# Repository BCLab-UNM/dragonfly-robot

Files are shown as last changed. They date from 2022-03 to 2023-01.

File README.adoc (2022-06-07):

= Dragonfly Build Guide

== Everything you need to build a Dragonfly Robot. 

https://github.com/BCLab-UNM/dragonfly-robot/blob/main/3DPrintedParts.adoc[3D Printed Parts]

https://github.com/BCLab-UNM/dragonfly-robot/blob/main/PurchasedPartsList.csv[Purchased Parts List]

https://github.com/BCLab-UNM/dragonfly-robot/blob/main/PhysicalBuild.adoc[Physical Build]

https://github.com/BCLab-UNM/dragonfly-robot/blob/main/SoftwareInstallationSetup.adoc[Software Installation & Setup]

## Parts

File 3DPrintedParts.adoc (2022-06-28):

= 3D Printed Parts

3D prints:

All prints are version controlled in onshape.
To generate STL files for Cura, onshape export to STL files using the following settings.  Note the Millimeter Units:

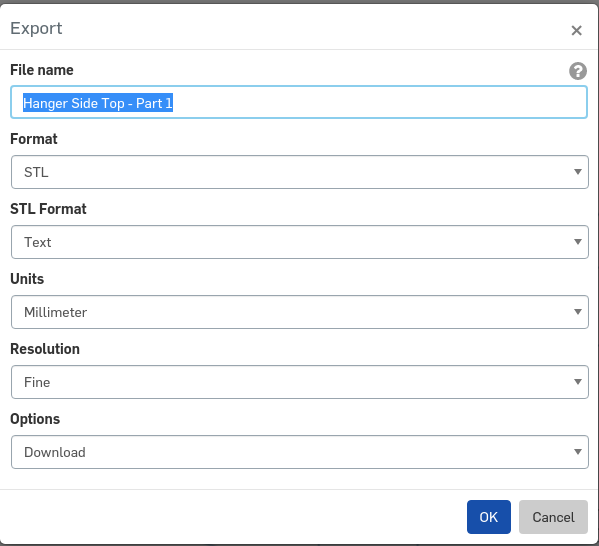
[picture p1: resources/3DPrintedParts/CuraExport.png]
Cura Export


Slice STL files with cura and print on lulzbot (lulzbot specific version of cura: https://www.lulzbot.com/cura)

== Part prints:
|===
|Part|Quantity|Picture|Notes

|Arms
|
|
|

|Arm Fulcrum
https://github.com/BCLab-UNM/dragonfly-robot/blob/main/resources/3DPrintedParts/stl/Arm%20Fulcrum.stl[STL]
|4
a|
|

|Arm Lock Lock
https://github.com/BCLab-UNM/dragonfly-robot/blob/main/resources/3DPrintedParts/stl/Arm%20Lock%20Lock.stl[STL]
|4
|
|

|ESC Mount
https://github.com/BCLab-UNM/dragonfly-robot/blob/main/resources/3DPrintedParts/stl/Motor%20Mount%20Top.stl[STL]
|4
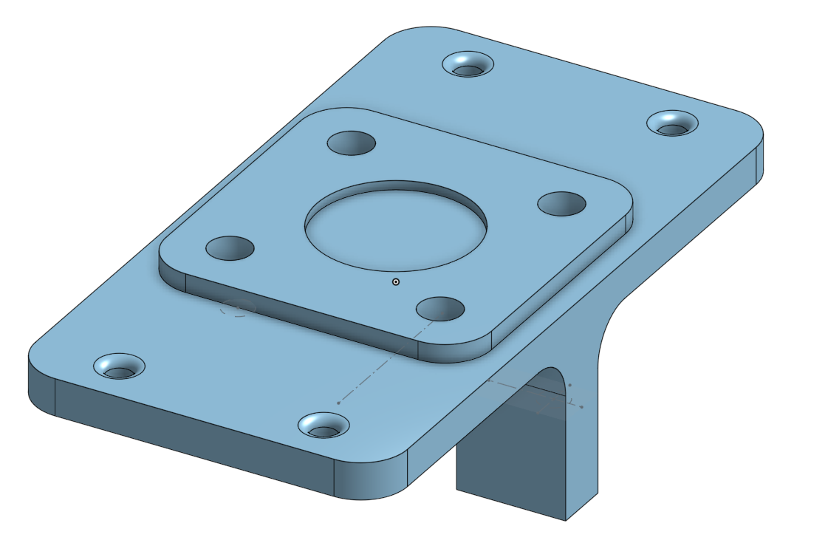
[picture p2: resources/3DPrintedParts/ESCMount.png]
a|
|

|Body
|
|
|

https://github.com/BCLab-UNM/dragonfly-robot/blob/main/resources/3DPrintedParts/stl/BH%20Clamp.stl[STL]

|Arm / Leg lock
https://github.com/BCLab-UNM/dragonfly-robot/blob/main/resources/3DPrintedParts/stl/Leg%20lock.stl[STL]
|6
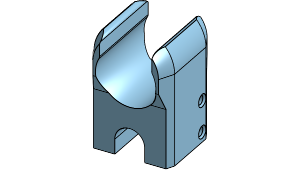
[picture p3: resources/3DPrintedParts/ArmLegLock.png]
a|
|

|Battery Tray
|
|
|

|Hanger side mount
https://github.com/BCLab-UNM/dragonfly-robot/blob/main/resources/3DPrintedParts/stl/Hanger%20Battery%20Plate.stl[STL]
https://github.com/BCLab-UNM/dragonfly-robot/blob/main/resources/3DPrintedParts/stl/Hanger%20Side%20Top.stl[STL]
|4
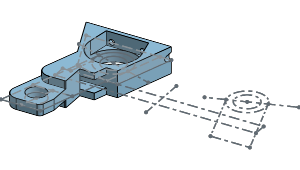
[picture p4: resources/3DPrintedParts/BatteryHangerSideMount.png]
a|
|Mirror 2 in Cura

|Hanger side bottom Left
https://github.com/BCLab-UNM/dragonfly-robot/blob/main/resources/3DPrintedParts/stl/Hanger%20Side%20Bottom%20-%20Part%201.stl[STL]
|1
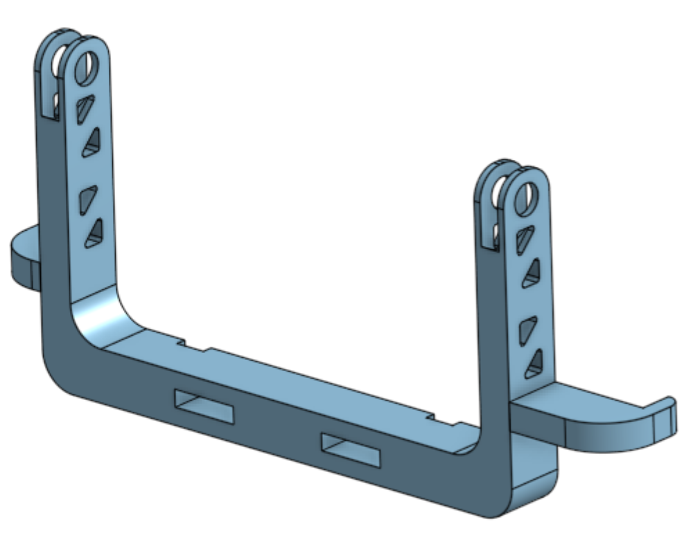
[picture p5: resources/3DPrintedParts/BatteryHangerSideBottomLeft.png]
a|
|

|Hanger side bottom Right
https://github.com/BCLab-UNM/dragonfly-robot/blob/main/resources/3DPrintedParts/stl/Hanger%20Side%20Bottom%20-%20Part%202.stl[STL]
|1
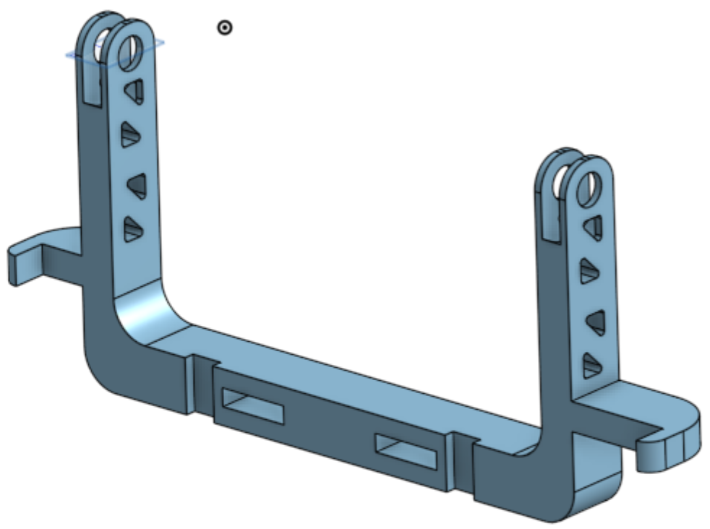
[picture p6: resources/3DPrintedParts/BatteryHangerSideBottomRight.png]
a|
|

|Axil
https://github.com/BCLab-UNM/dragonfly-robot/blob/main/resources/3DPrintedParts/stl/Axil.stl[STL]
|4
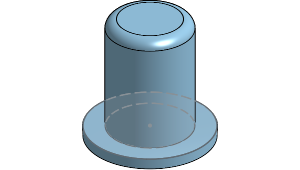
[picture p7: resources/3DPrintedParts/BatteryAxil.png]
a|
|

|Hanger brace and bracket
|2
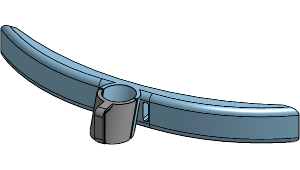
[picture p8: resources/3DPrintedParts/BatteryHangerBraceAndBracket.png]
a|
|

|Crossbeam
https://github.com/BCLab-UNM/dragonfly-robot/blob/main/resources/3DPrintedParts/stl/Cross%20Beam.stl[STL]
|2
a|
|

|Flight Controller Mount
https://github.com/BCLab-UNM/dragonfly-robot/blob/main/resources/3DPrintedParts/stl/Flight%20Controller%20-%20Top.stl[STL]
|
a|
|

|Flight controller Bottom mount
https://github.com/BCLab-UNM/dragonfly-robot/blob/main/resources/3DPrintedParts/stl/Flight%20Controller%20-%20Bottom.stl[STL]
|1
a|
|

|GPS Mount
|
|
|

|Bottom
|1
a|
|

|Screw-down
|1
a|
|

|Arm bottom
|1
a|
|Arm bottom should be cut down to allow for GPS cable to each and be able to be folded

|Arm top
|1
a|
|

|Mast stiffener
|1
a|
|

|Other
|
|
|

|Lidar mount
https://github.com/BCLab-UNM/dragonfly-robot/blob/main/resources/3DPrintedParts/stl/LIDAR%20Lite%20v4%20HP%20Holder.stl[STL]
|1
a|
|

|===

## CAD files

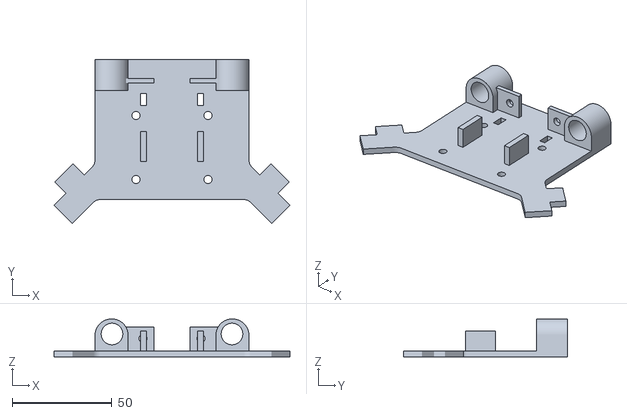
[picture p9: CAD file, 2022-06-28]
resources/3DPrintedParts/stl/LIDAR Lite v4 HP Holder.stl
118.0 x 82.0 x 19.0

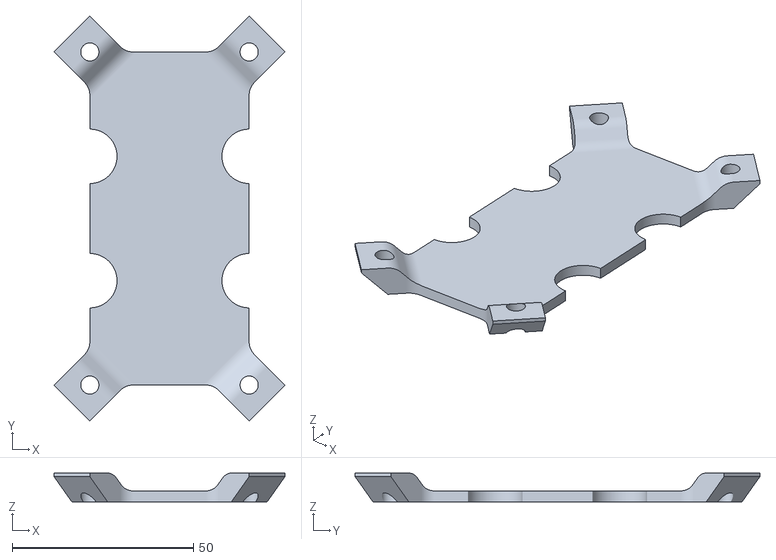
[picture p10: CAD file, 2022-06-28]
resources/3DPrintedParts/stl/Flight Controller - Bottom.stl
63.8 x 111.8 x 8.00

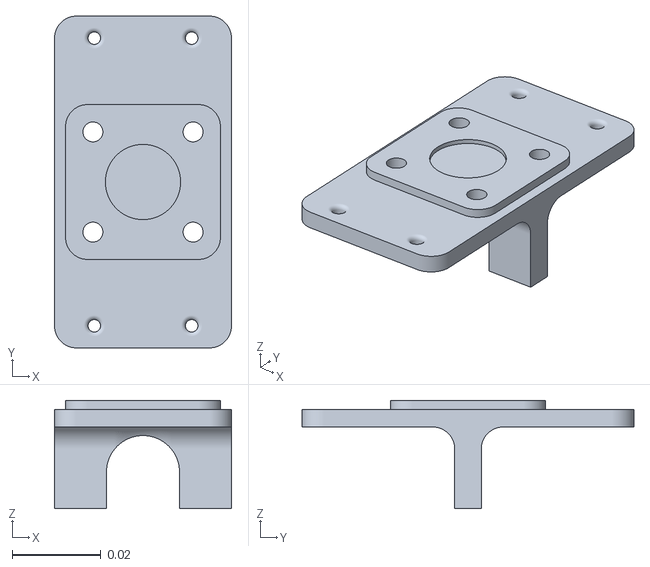
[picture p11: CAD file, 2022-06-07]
resources/3DPrintedParts/stl/Motor Mount Top.stl
0.04 x 0.075 x 0.0244

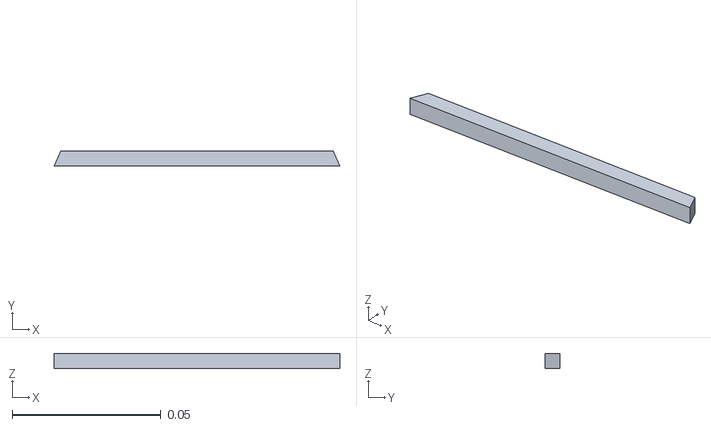
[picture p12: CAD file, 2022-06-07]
resources/3DPrintedParts/stl/Cross Beam.stl
0.0962 x 0.0052 x 0.005

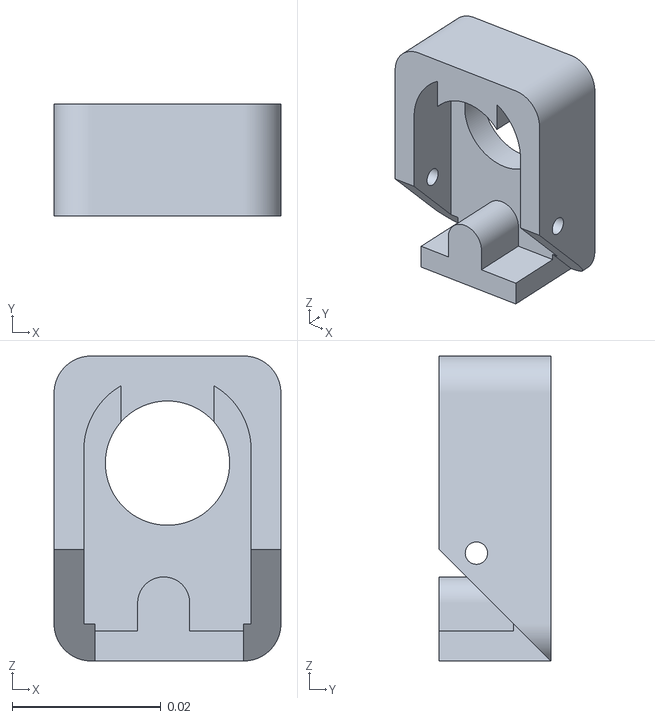
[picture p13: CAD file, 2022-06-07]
resources/3DPrintedParts/stl/Arm Lock Lock.stl
0.0305 x 0.015 x 0.041

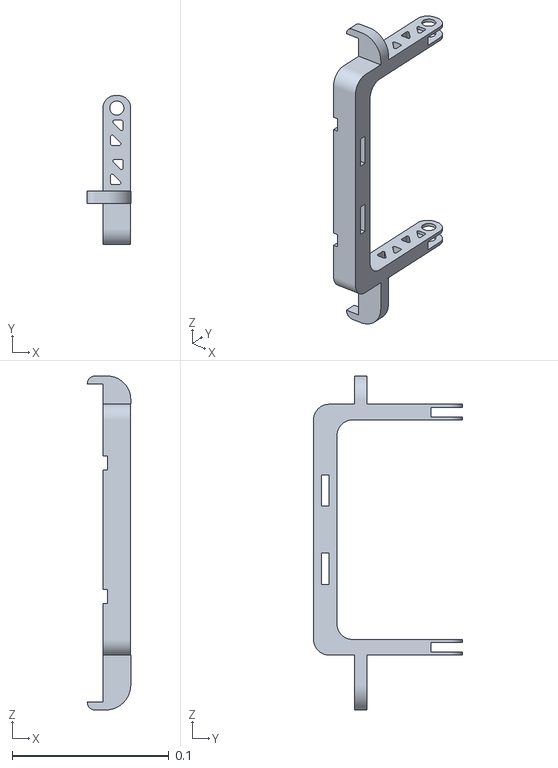
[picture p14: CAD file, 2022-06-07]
resources/3DPrintedParts/stl/Hanger Side Bottom - Part 2.stl
0.0278 x 0.095 x 0.213

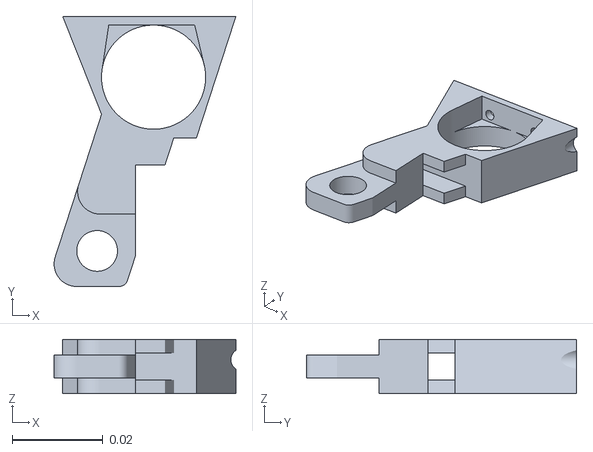
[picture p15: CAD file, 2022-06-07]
resources/3DPrintedParts/stl/Hanger Side Top.stl
0.0402 x 0.0597 x 0.012

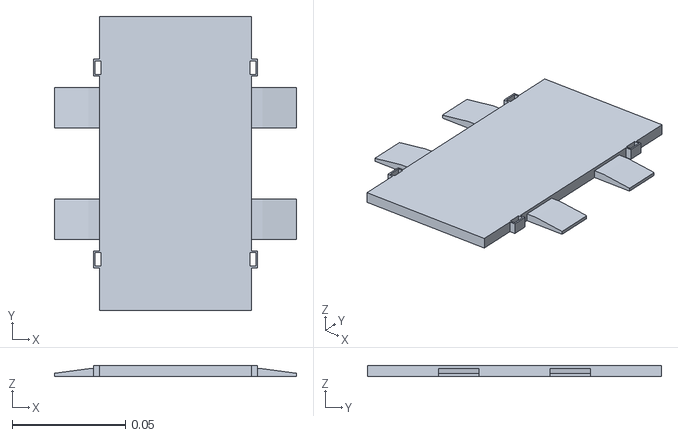
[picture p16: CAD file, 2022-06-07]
resources/3DPrintedParts/stl/Hanger Battery Plate.stl
0.107 x 0.13 x 0.005

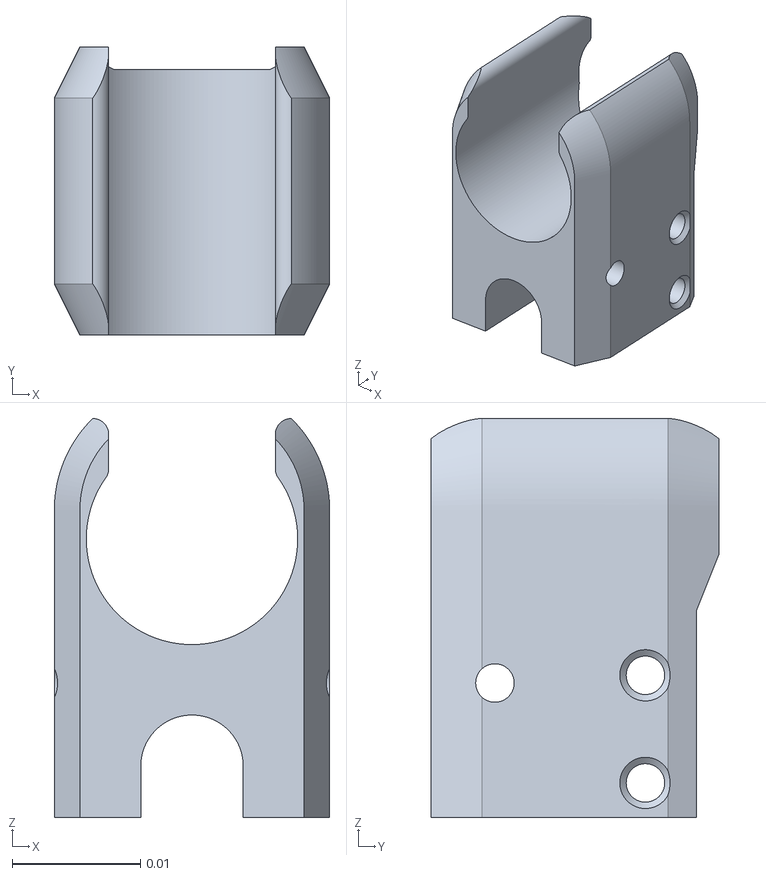
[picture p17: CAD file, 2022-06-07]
resources/3DPrintedParts/stl/Leg lock.stl
0.0215 x 0.0225 x 0.0312

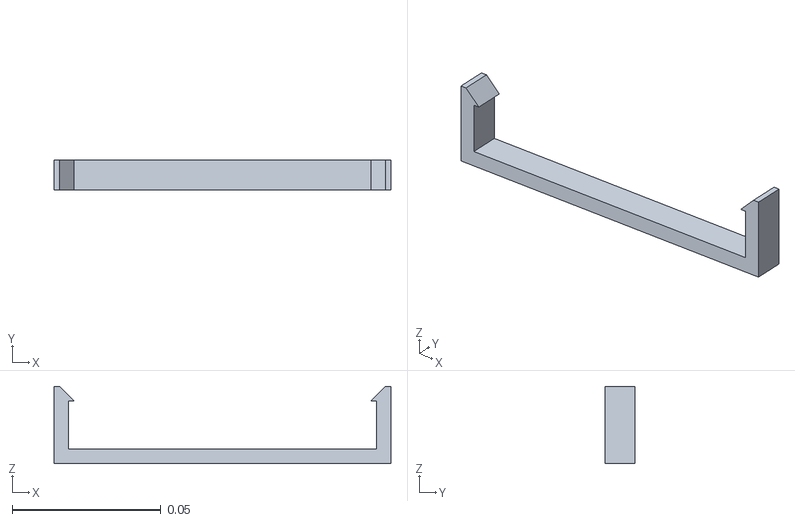
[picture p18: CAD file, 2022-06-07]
resources/3DPrintedParts/stl/BH Clamp.stl
0.113 x 0.01 x 0.026

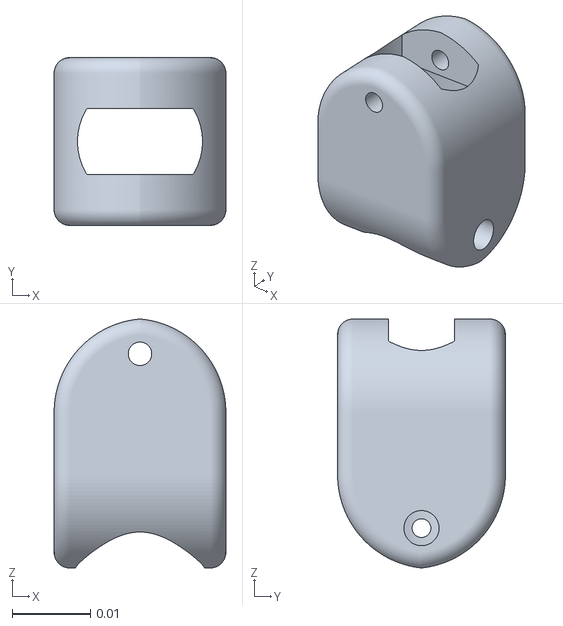
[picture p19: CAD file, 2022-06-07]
resources/3DPrintedParts/stl/Arm Fulcrum.stl
0.022 x 0.0215 x 0.0319

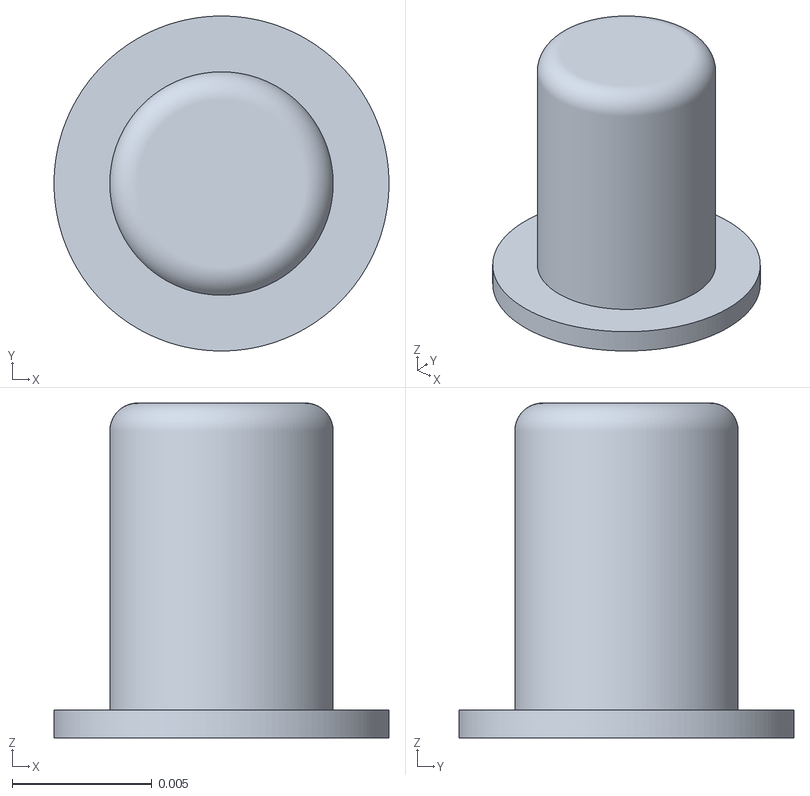
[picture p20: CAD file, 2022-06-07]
resources/3DPrintedParts/stl/Axil.stl
0.012 x 0.012 x 0.012

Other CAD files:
resources/3DPrintedParts/stl/Hanger Side Bottom - Part 1.stl

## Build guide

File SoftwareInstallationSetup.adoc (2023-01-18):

== Download and install the Raspberry Pi Imager
https://www.raspberrypi.com/software/

Ubuntu: https://downloads.raspberrypi.org/imager/imager_latest_amd64.deb

Windows: https://downloads.raspberrypi.org/imager/imager_latest.exe

== Download the image
https://cdimage.ubuntu.com/releases/22.04.1/release/ubuntu-22.04.1-preinstalled-desktop-arm64+raspi.img.xz
or #@TODO test drivers and boot time between them
https://cdimage.ubuntu.com/releases/22.04.1/release/ubuntu-22.04.1-preinstalled-server-arm64+raspi.img.xz

=== Run the Raspberry Pi Imager
Then click "CHOOSE OS" under Operating System then "use custom" then select the `ubuntu-22.04.1-preinstalled-desktop-arm64+raspi.img.xz`
Then click "CHOOSE STORAGE" under Storage and then "Internal SD card reader"
Click "WRITE" enter your password if it promts you.

Profit

After writing is compleate, mount it and edit its /etc/hostname & /etc/hosts files

=== @NOTE where it is `#` please put the appropriate number
== Edit `/etc/hostname`
edit to just
`dragonfly#`

== Edit `/etc/hosts`
just below localhost paste
`127.0.1.1 dragonfly#`

== Boot the pi up and change the password(will prompt you to do it on login),

= On the laptop/desktop

== Install ansible

== Copy over your public ssh key
from the laptops `.ssh/id_rsa.pub`
insert into `.ssh/authorized_keys`
or just run `ssh-copy-id ubuntu@dragonfly's_ip`
or just run `ssh-copy-id ubuntu@dragonfly#.local`

@Note `dragonfly#.local` might resolve

== Run the playbook from the dragonfly-controller/scripts directory
`ansible-playbook playbook.yaml -u ubuntu --inventory ./inventory`

@Note if you are getting this error below it is probably because unattended upgrades are in progress, so just wait a few minutes and run it again.

[source]
----
fatal: [dragonfly#.local]: FAILED! => {"changed": false, "msg": "'/usr/bin/apt-get upgrade --with-new-pkgs ' failed: E: Could not get lock /var/lib/dpkg/lock-frontend. It is held by process 2551 (unattended-upgr)\nE: Unable to acquire the dpkg frontend lock (/var/lib/dpkg/lock-frontend), is another process using it?\n", "rc": 100, "stdout": "", "stdout_lines": []}

----

= Install Mission Planner on Windows
https://ardupilot.org/planner/docs/mission-planner-installation.html

Connect Pixhawk to computer via USB cable

Flash Arducopter firmware and restart

Copy initial parameters from another Dragonfly and restart

Verify battery voltage.  If the battery voltage is too low (11V?) then you may need to recopy in the initial parameters.

Without propellers installed, perform a motor test.  Verify correct motor orientation and spin (reference above figure)

= Install Mission Planner on Linux (Currently broken)
Make sure exicute from inside a sub directory
[source,bash]
----
sudo apt install mono-runtime libmono-system-windows-forms4.0-cil libmono-system-core4.0-cil libmono-system-management4.0-cil libmono-system-xml-linq4.0-cil
sudo apt install mono-complete
wget https://firmware.ardupilot.org/Tools/MissionPlanner/MissionPlanner-latest.zip
unzip MissionPlanner-latest.zip
mono MissionPlanner.exe
----

= Transmitters
## Download the companion applicaiton
https://www.open-tx.org/downloads click the most recent at the top then scroll to the bottom and under `Download links:` click the appropriate installer for your system. 

== Download the SD card image
https://downloads.open-tx.org/2.3/release/sdcard/opentx-t16/

== Verify a usb connection with the transmitter
Plug in the transmitter's micro usb if you are running linux run `lsusb | grep "DFU Mode"` to verify it has come up properly if not disassemble and inspect/reseat the ribbon cable
If all is good you should see this `Bus 001 Device 036: ID 0483:df11 STMicroelectronics STM Device in DFU Mode`

== Install the downloaded opentx companion applicaiton
add the radio profile 
Radio type: Jumper T16
We have a mixture of radios so if the antenna is on the upper front then select `internalmulti` if there is the module installed below don't have it selected.
You can select `noheli` as we are running quads nto helicopters.

On the leftside make sure to download a copy of the original firmware and save it.
Make sure to click `show details` and read as you will get a `Flashing done` message even when it fails

Then `Write Firmware to radio` again make sure that the `show details` checkbox is checked and read the output to make sure the flashing completed

Unplug the transmitter and remove the sd card, make a copy of its contents, wipe it clean and then write to it the extracted files from what you downloaded in part `Download the SD card image`

Reinstall the SD card and power up the transmitter and calibrate the analogs

=== External antenna module
In the case of TX1 it does not have an internal module and the external module was running an old bootloader that did not support upgrading the firmware from the transmitter.
So Plug directly into the external module's USB micro at the bottom the the transmitter and plug into a linux system
Run `lsusb` you should see something like `Bus 001 Device 045: ID 10c4:ea60 Silicon Labs CP210x UART Bridge`

Download the module's new firmware
https://github.com/pascallanger/DIY-Multiprotocol-TX-Module/releases/download/v1.3.3.7/mm-stm-serial-reta-v1.3.3.7.bin
For a current list go to 
https://downloads.multi-module.org/

==== Install Flash multi
Fallow the instructions on
https://github.com/benlye/flash-multi/blob/master/doc/Linux.md

You'll end up running something like

[source,bash]
----
wget https://github.com/benlye/flash-multi/releases/download/0.6.1/flash-multi-0.6.0.tar.gz
tar -xvzf flash-multi-0.6.0.tar.gz
cd flash-multi-0.6.0
sudo ./tools/install.sh
sudo cp -v ./tools/45-maple.rules /etc/udev/rules.d/45-maple.rules
sudo chown root:root /etc/udev/rules.d/45-maple.rules
sudo chmod 644 /etc/udev/rules.d/45-maple.rules
sudo udevadm control --reload-rules
sudo usermod -a -G plugdev $USER\nsudo usermod -a -G dialout $USER
----
`./flash-multi -f /home/carter/Downloads/mm-stm-serial-reta-v1.3.3.7.bin -p /dev/ttyUSB0`

Once you are running a more modern bootloader on the external module you can update the using the transmitter
Just copy the bin file to the onboard SD card and fallow this
https://www.multi-module.org/using-the-module/firmware-updates/update-methods#opentx

== Rebind the transmitter to the dragonflys
Hit the "MDL" button, then roll the right roller to the right until you get to Internal(or External) RF got to mode change to `MULTI`, the next option change to `FrSky X` then the next selection to `D16 8ch` press the wheel for enter/continue
Then change the receiver number to match the dragonfly's # and then select bind, the transmitter should beep. While you are doing this power up the dragonfly and while doing so have the small button the on the X8R depressed.
then power cycle both the dragonfly and the transmitter you should have a solid green light on the X8R receiver if not try again

== Disable inactivity alarm 
Sys press the page button until you are on the Radio setup tab then scroll down to alarms and set inactivity to `0m`

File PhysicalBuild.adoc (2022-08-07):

= PhysicalBuild
:toc:

== Tiger Motor Flame 60A ESC programing cable removal mod
Using a 1.5mm hex tool unscrew the 4 bolts

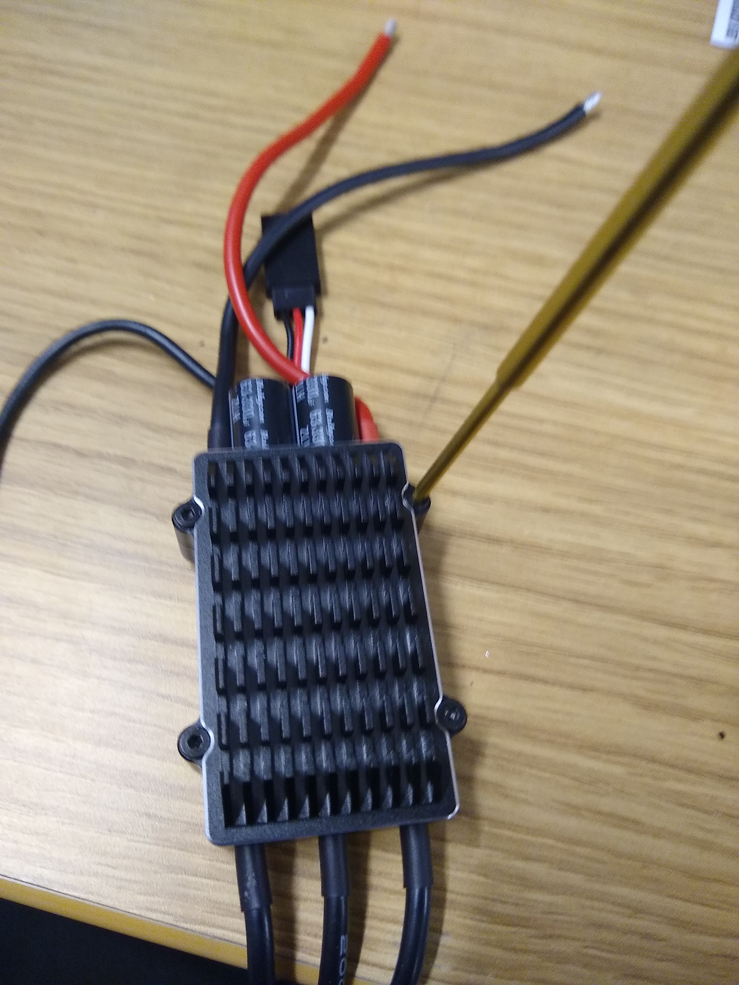
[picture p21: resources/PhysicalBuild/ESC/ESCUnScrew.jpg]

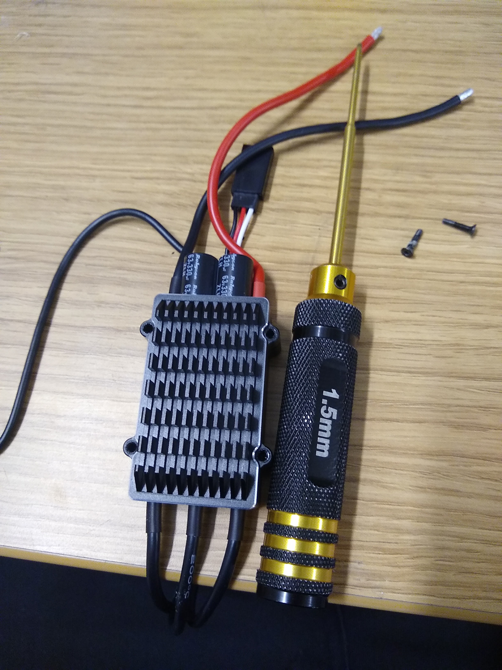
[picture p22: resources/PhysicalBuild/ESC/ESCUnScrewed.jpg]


The housing should pull apart smoothly, and then carefully pick off the indicated epoxy.

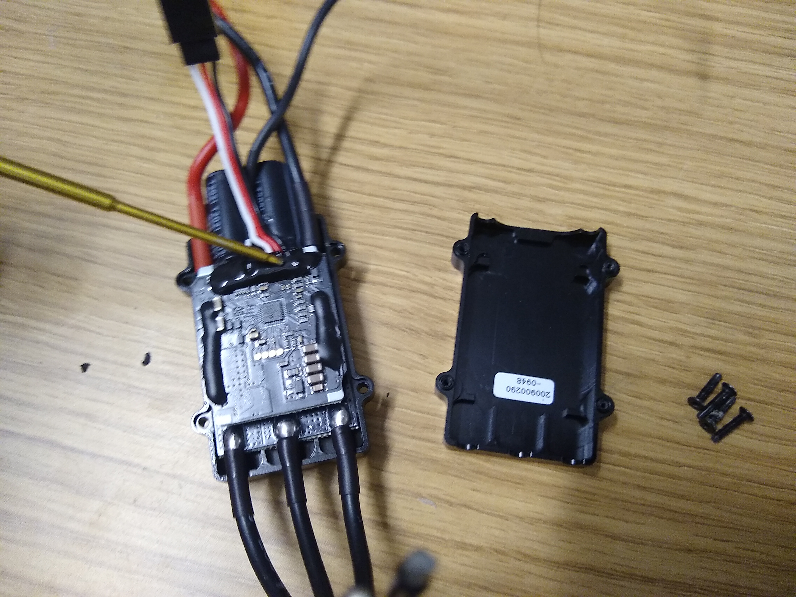
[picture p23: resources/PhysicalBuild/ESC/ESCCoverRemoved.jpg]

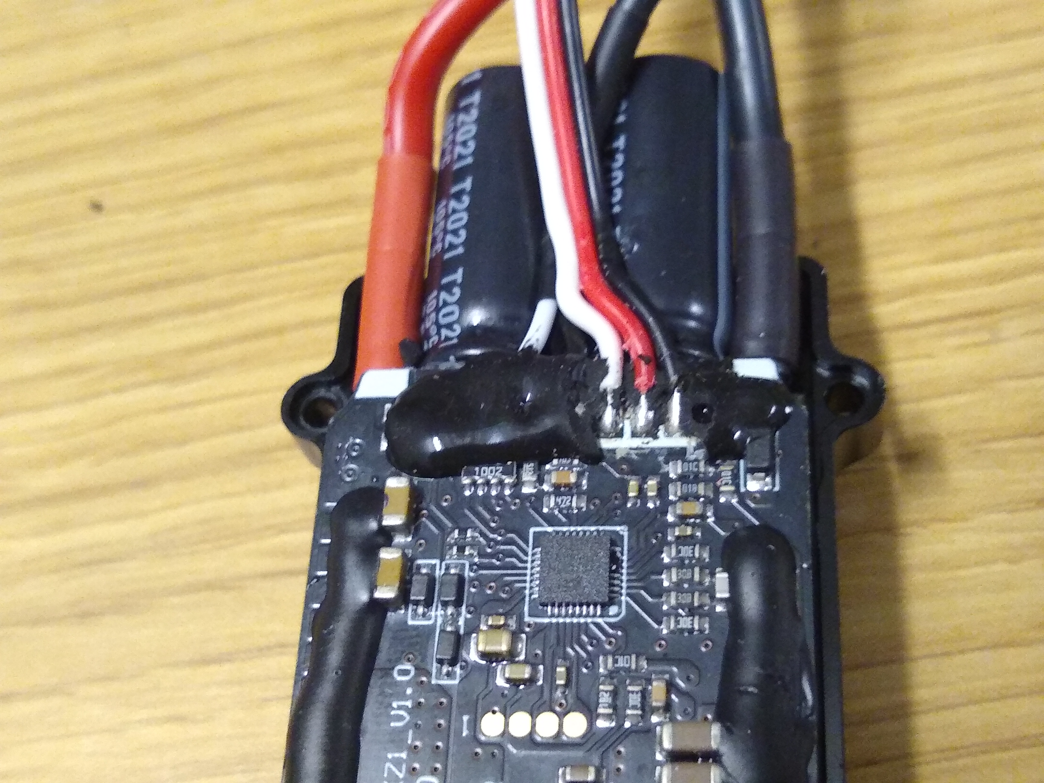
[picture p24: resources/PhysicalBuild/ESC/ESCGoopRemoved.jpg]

Use a soldering iron to reflow and remove the indicated wires, then cover the pads with hotglue.

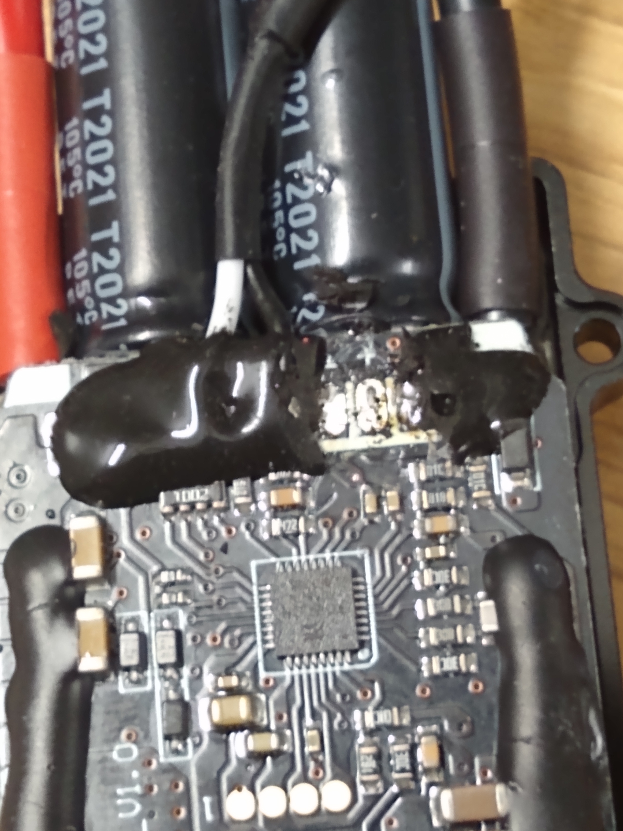
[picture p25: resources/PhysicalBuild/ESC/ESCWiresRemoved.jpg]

While the hotglue is still got place the back cover back on firmly and hold for a few seconds to cool.

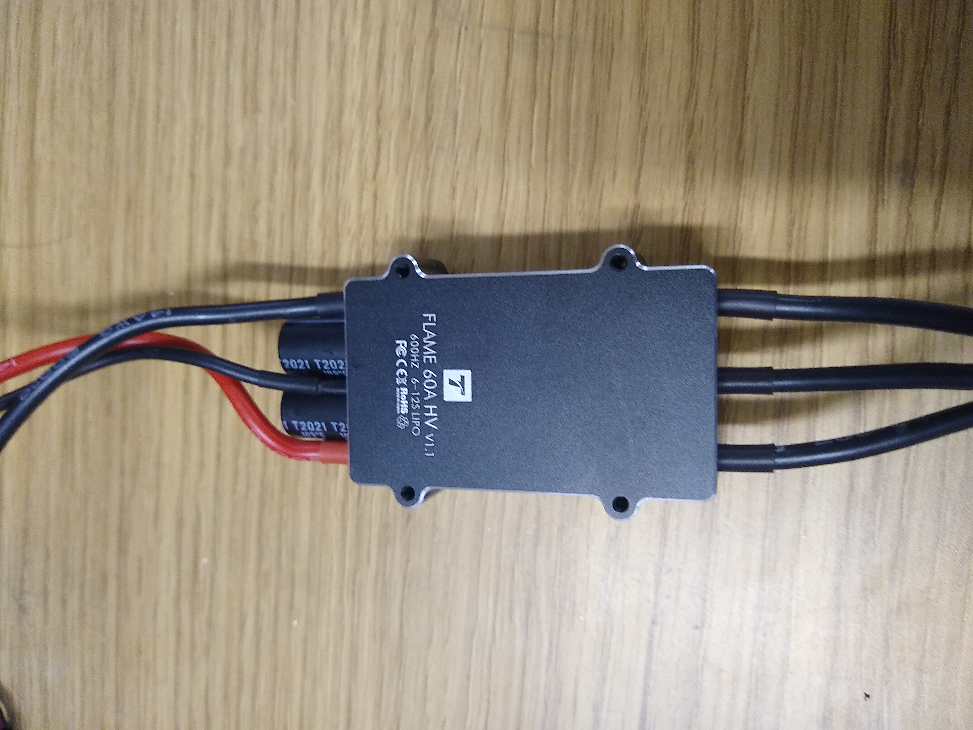
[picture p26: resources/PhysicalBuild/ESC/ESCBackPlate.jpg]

Flip back over and reinstall the bolts.

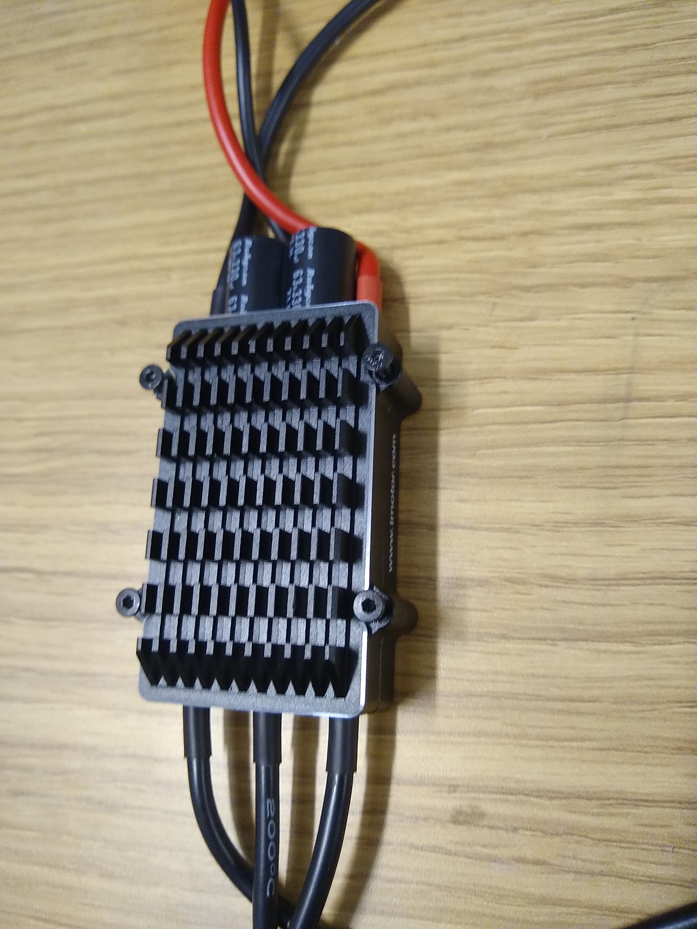
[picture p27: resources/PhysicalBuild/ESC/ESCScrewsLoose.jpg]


== Arms

Solder motors to ESCs

* 2 motors straight wired, 2 motors with 2 wires swapped.  This supports the motor orientation to hard-wire their rotation.  Make sure to add heat shrink around each solder joint.

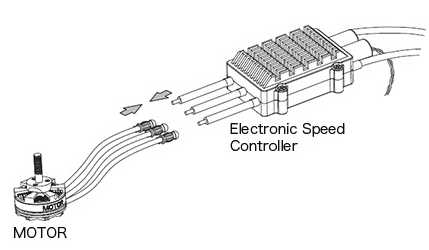
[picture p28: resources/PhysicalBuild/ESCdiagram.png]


Extend power wires from ESCs

* Add heat shrink around each solder joint



Attach Motor to motor mounts

* Make sure to attach metal brackets prior to attaching motors
* Loctite motor bolts and arm bracket bolds

Slide the plastic onto the bolt

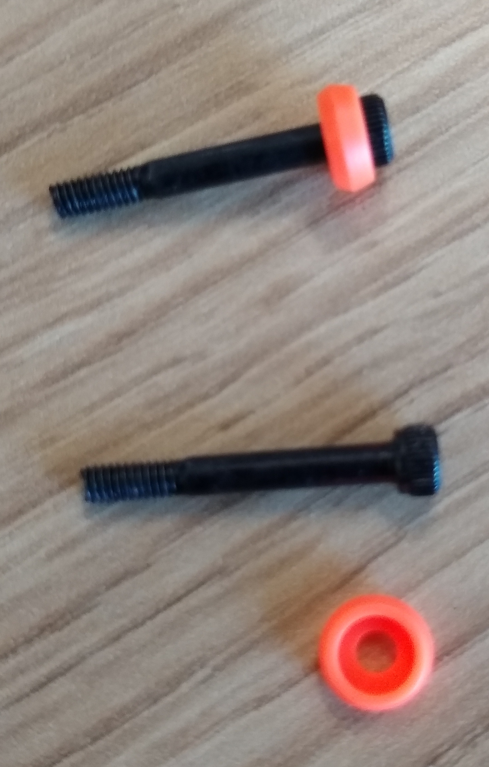
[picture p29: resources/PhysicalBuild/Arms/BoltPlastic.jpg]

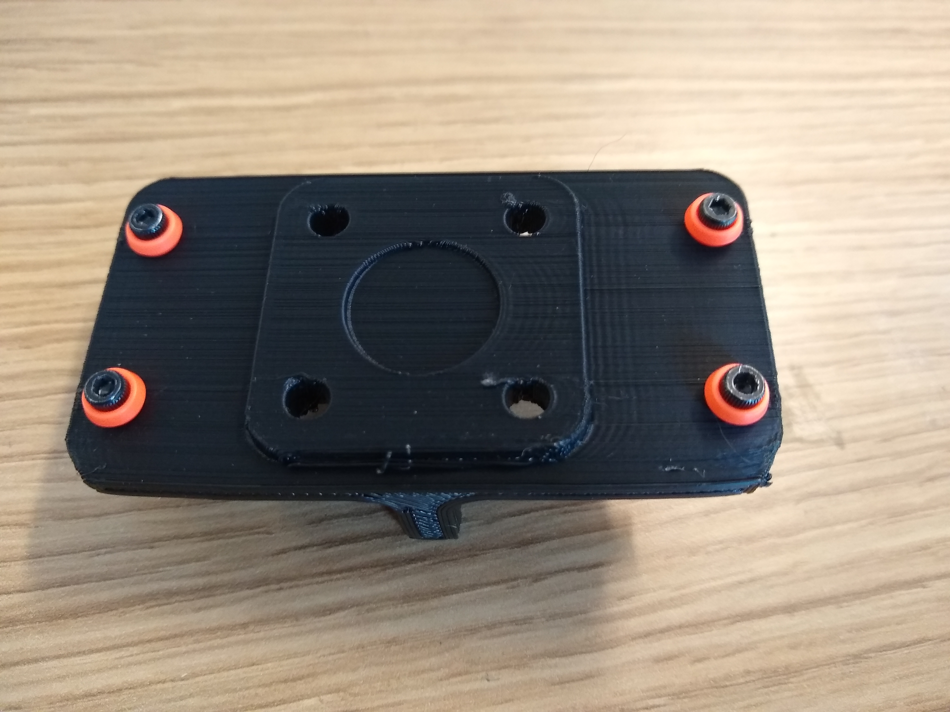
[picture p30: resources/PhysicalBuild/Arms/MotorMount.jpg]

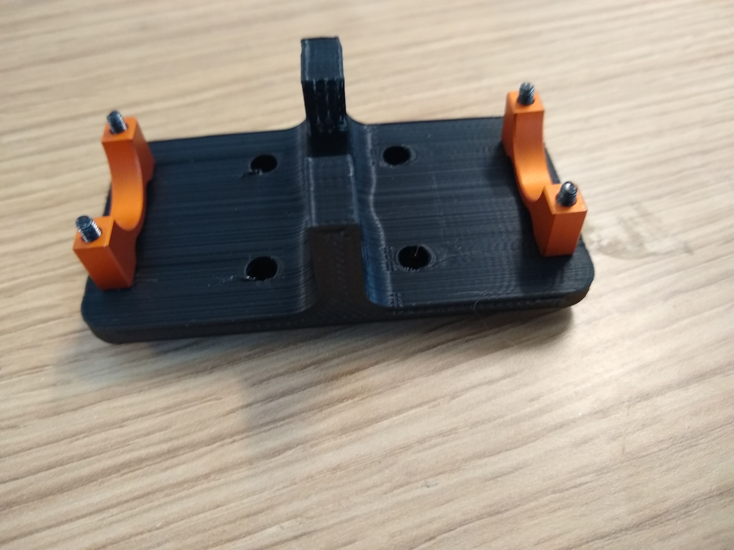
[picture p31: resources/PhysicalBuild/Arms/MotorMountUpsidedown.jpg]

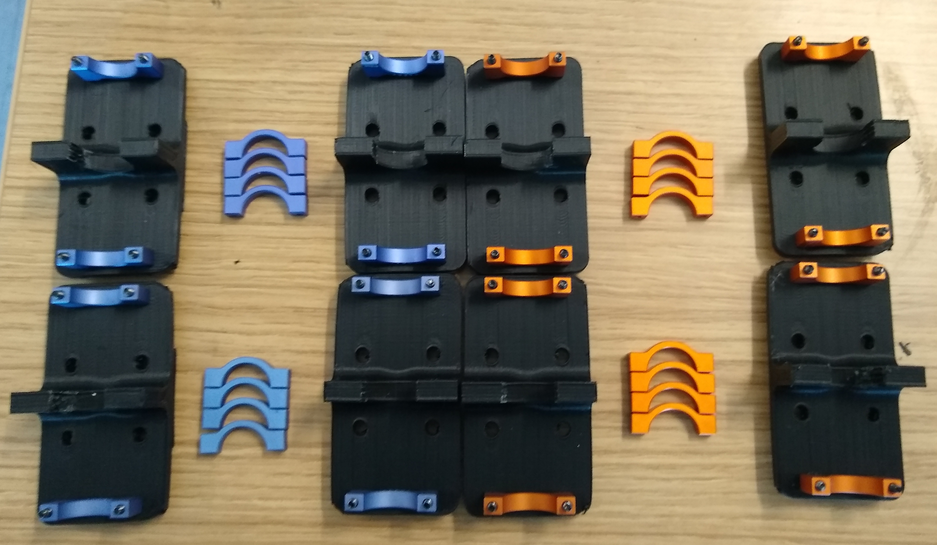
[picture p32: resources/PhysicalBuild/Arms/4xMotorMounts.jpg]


`@TODO update image`



NOTE: Wear respiration PPE when cutting or drilling carbon fiber.

Cut arm to 18 inches:



Drill a hole to attach the hinge to arm.  This hole should align with the hinge mounting holes -  to align in, you can put the hinge in place and mark a drill point.



Prepare the arm hinge 3D print by adding the brass inserts. Note the shorter brass insert is used to secure the long bolt through the arm, all the other brass inserts are the longer inserts.




Remove the bolt from the kit arms:

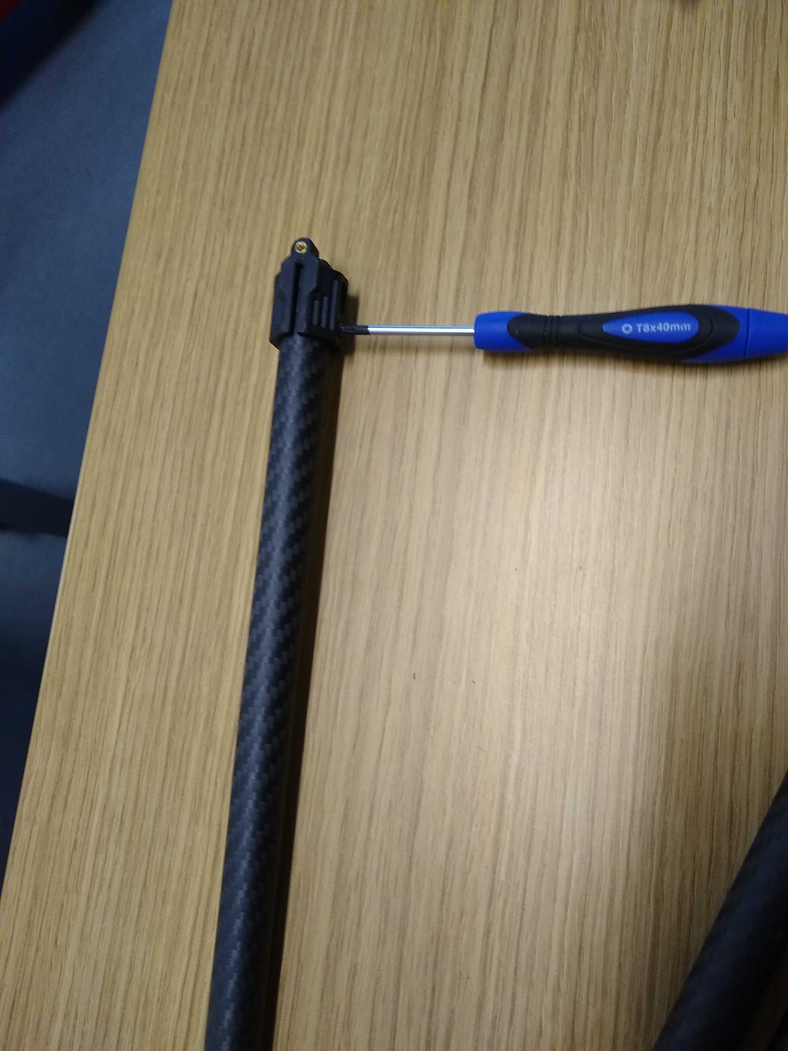
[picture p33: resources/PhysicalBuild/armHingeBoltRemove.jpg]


Attach the prepared arm hinge using the long bolt to the end of the arm:



Attach mounted motors to end of arms

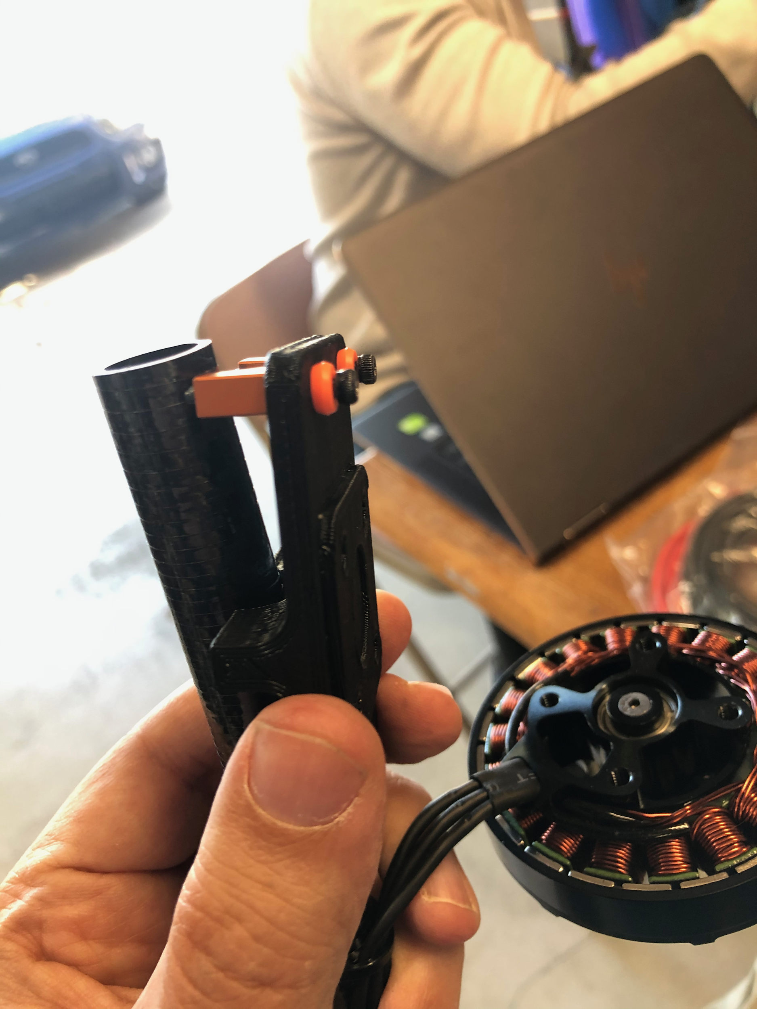
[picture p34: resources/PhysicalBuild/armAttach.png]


Zip tie ESCs to the bottom of the arm and the wires against the arms:

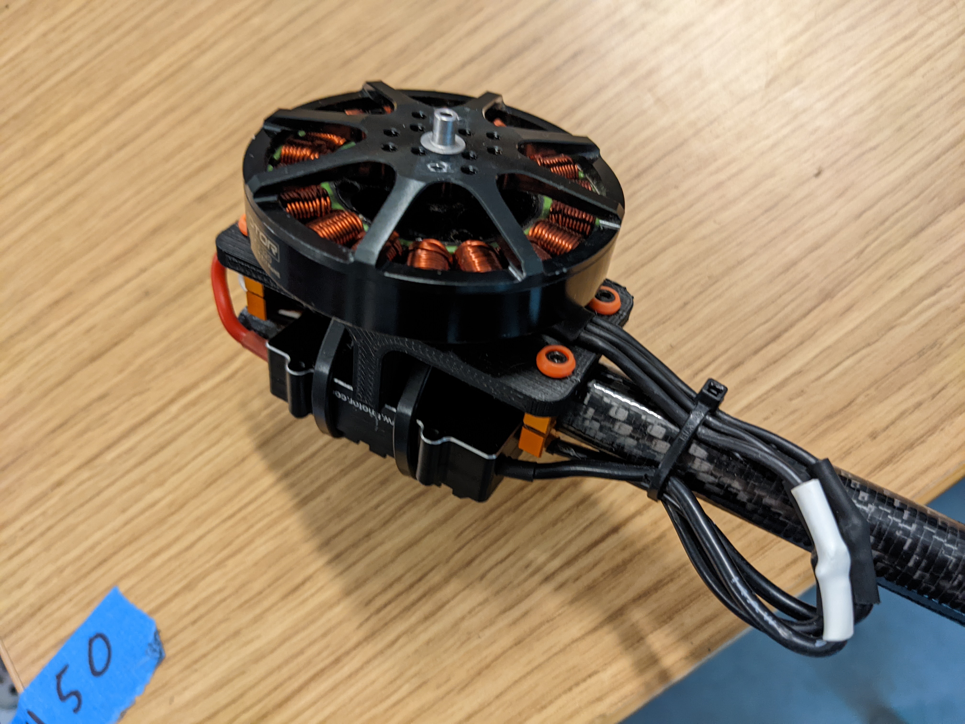
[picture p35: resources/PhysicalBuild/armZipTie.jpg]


Result
4x of these, 2 with swapped ESC / Motor wires:

`@TODO image of finished arms`

== Body

=== Legs
Cut the thicker carbon fiber tube to match the length of the provided ones in the kit.
Make sure the setscrews are installed if not look for them in a small plastic bag.
Install the tube and tighten till the tubes won't move/pullout.

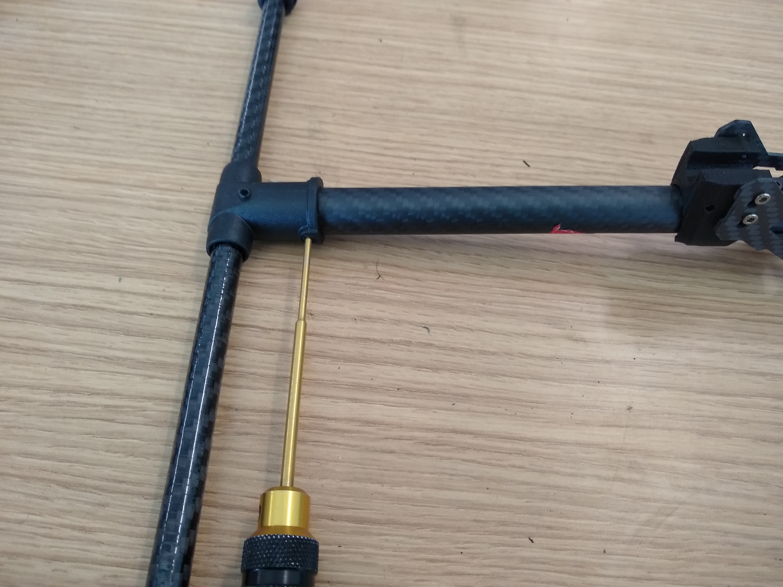
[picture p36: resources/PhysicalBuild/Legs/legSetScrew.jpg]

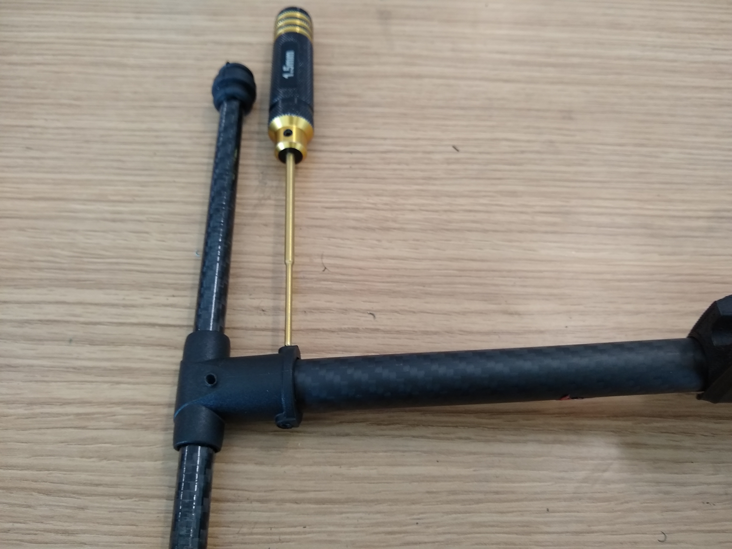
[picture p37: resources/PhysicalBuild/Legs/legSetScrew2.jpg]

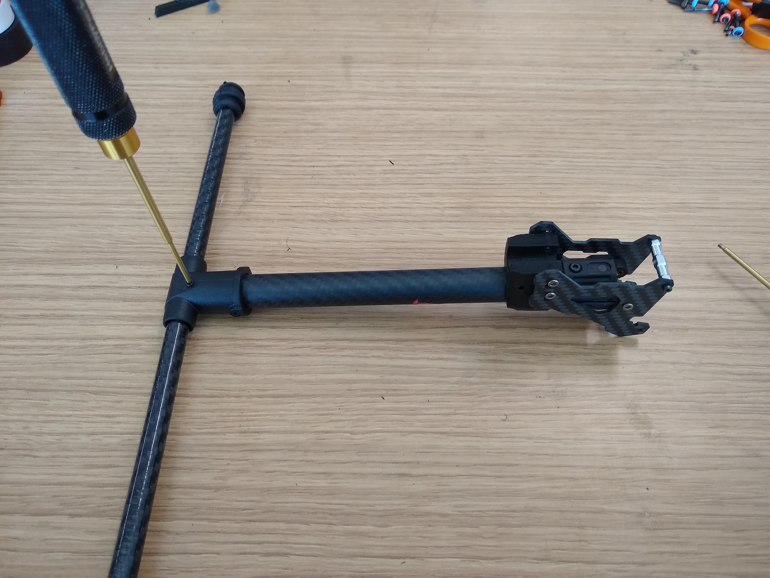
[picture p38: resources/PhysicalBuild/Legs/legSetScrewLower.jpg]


Mount Legs

Unscrew leg brackets and attach them to the body

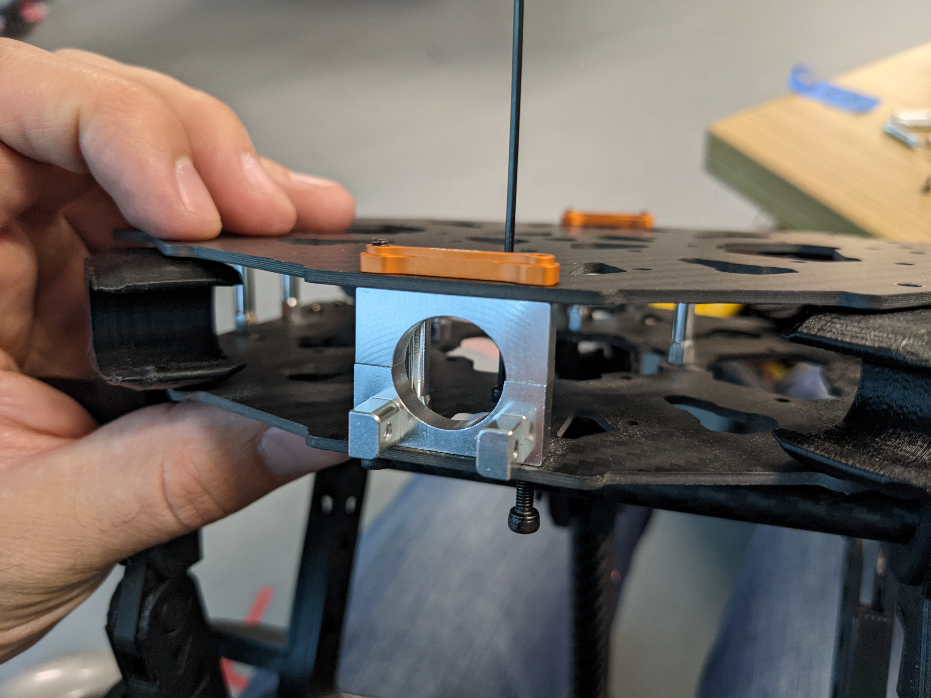
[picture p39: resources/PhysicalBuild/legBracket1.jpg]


Reattach legs to brackets and connect set screw

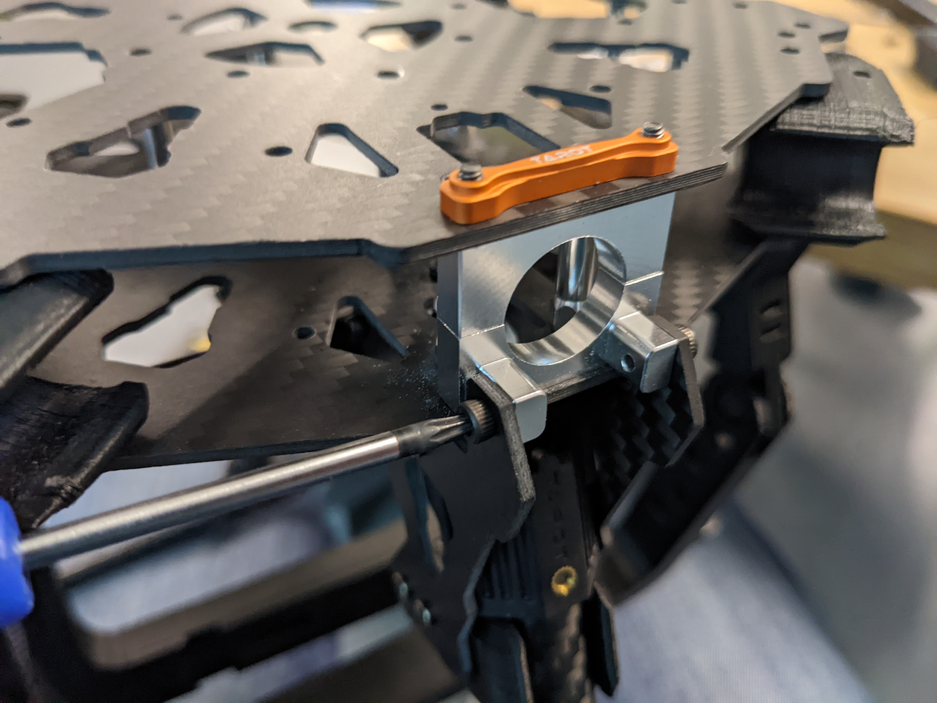
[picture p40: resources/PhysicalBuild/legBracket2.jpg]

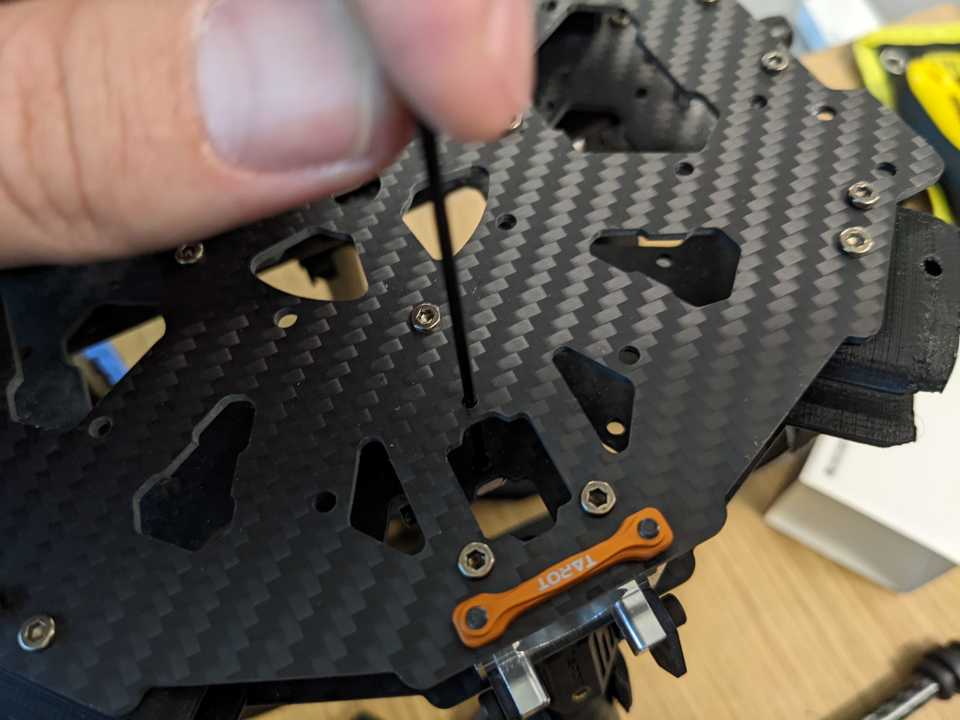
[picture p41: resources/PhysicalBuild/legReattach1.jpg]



Mount Arms

Prepare 3D printed arm clasps by inserting long brass inserts into mounting holes:

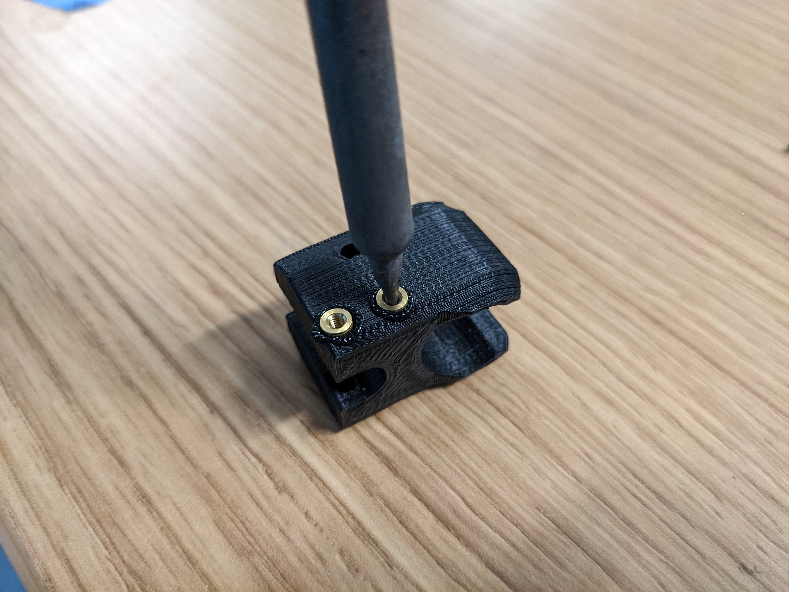
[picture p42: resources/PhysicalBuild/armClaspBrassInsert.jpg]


* Replace stock tarot frame arm locks with larger 3D printed arm clasps.


Attach built arms to attachment points in the body frame.



`@TODO missing image built arm attach`

Keep in mind motor orientation.  Motors A and C (1 and 2) should be using crossed ESC to motor wiring orientation, motors B and D should be straight. (See Quad motor letter example figure for arm labels).

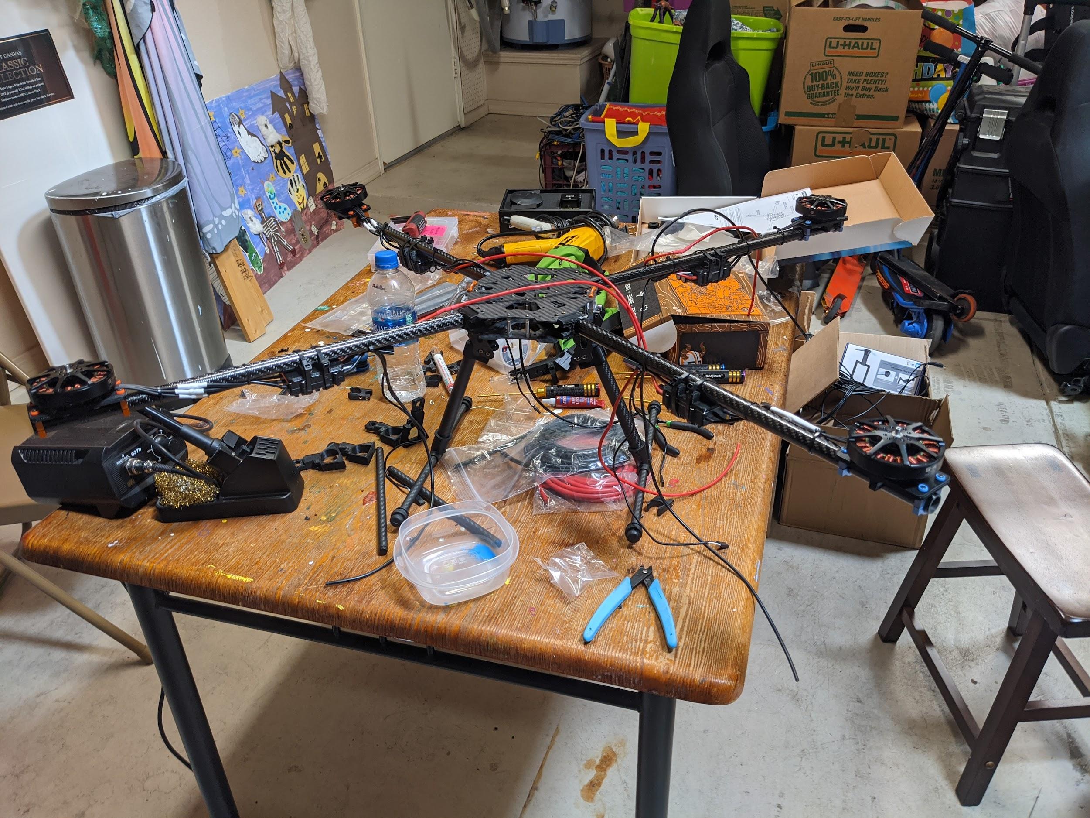
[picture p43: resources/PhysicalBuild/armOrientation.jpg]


Solder Hall Effect sensor (Mauch voltage sensor) to XT90 plug
Verify hall effect sensor orientation.  Arrow should be pointing away from the battery in, towards the quad

`@TODO missing image hall effect sensor`

Wire power to main power
Route wires into permanent locations and make sure you have enough slack
Hall Effect

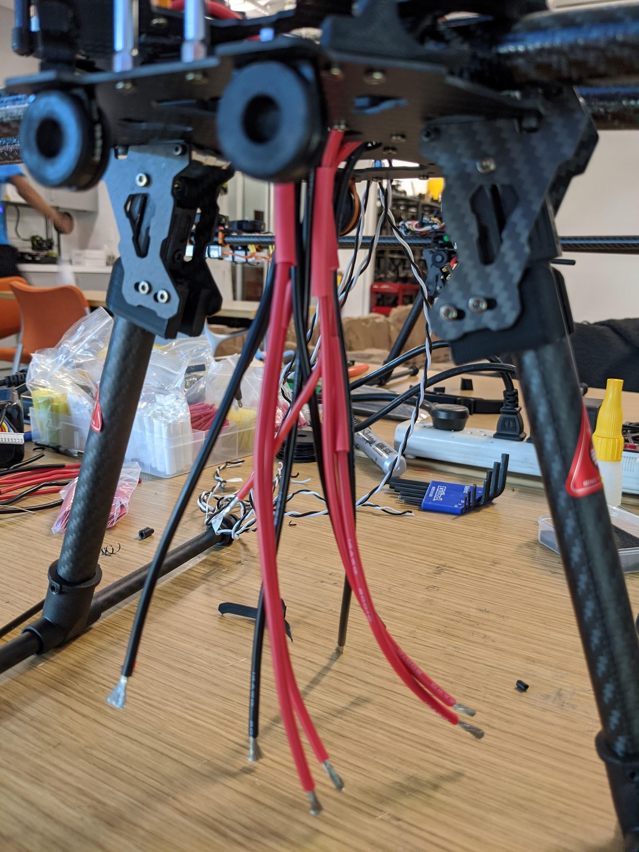
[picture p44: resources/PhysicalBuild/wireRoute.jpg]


5 power and 5 ground into 1 power 1 ground -> PL-Sensor -> Anti-spark connectors.  Add heavyduty heat shrink around joints and stow wires


Result:

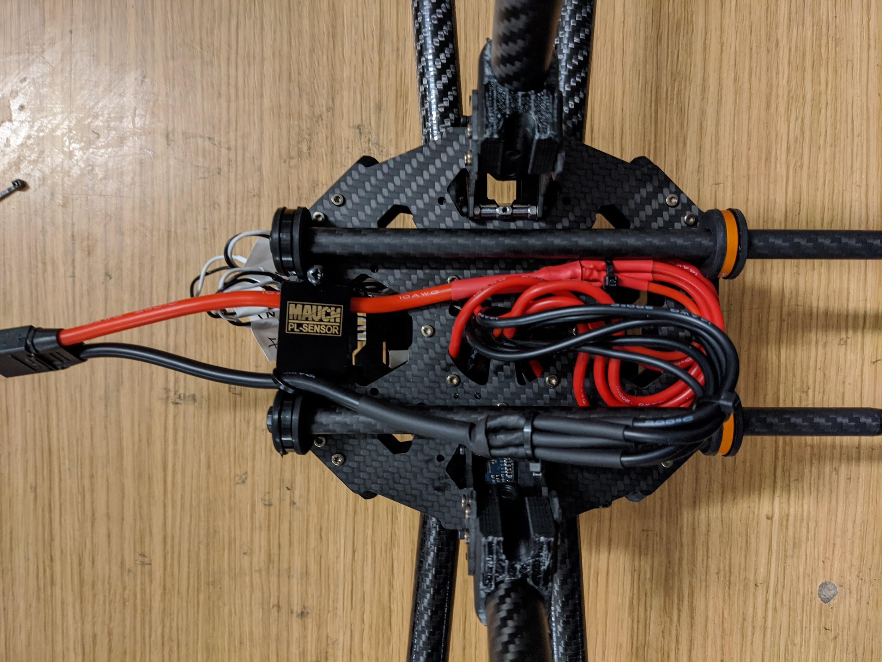
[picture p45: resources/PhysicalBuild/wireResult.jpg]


==  Battery Tray
Add Battery Tray
Attach tray hangers to body (metal payload brackets go inside of 3D printed parts):
`@TODO need image`

Add payload rails.  The long bracket end should face towards the back of the quad (weight offsets the payload)

`@TODO need image`

Attach left and right battery brackets using axils and crossbeams to stabilize separation between tray hangers.  Use a battery to ensure that the mounting separation is correct.  The battery should be fixed (not tight or loose) within the battery hangers and brackets.


Add glue to axils and crossbeams




`@TODO need image of adding glue to axils`

Mount top plate to body
Top plate should face forward with mourning fins on the left and right side of the quad.  The forward orientation of the plate has a notch for GPS mast clearance.

Make sure Mauch has enough slack

`@TODO missing image Mauch slack check`

Widen holes in body to accept bolt

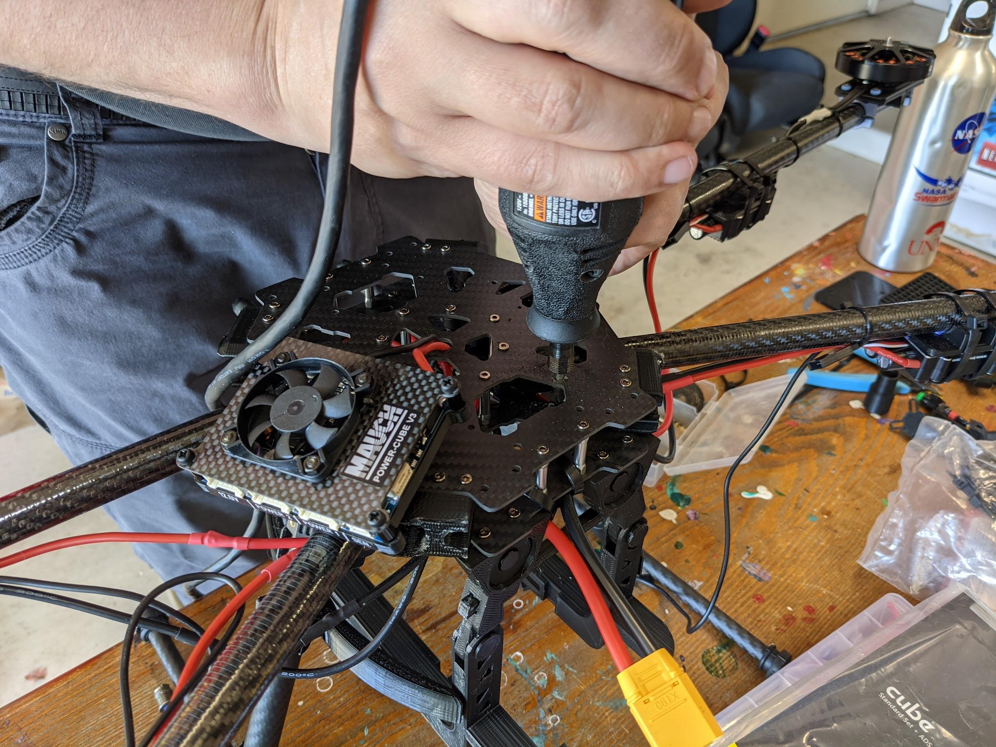
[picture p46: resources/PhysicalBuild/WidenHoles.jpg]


Screw top plate to body with rubber dampeners sandwich between top plate and body


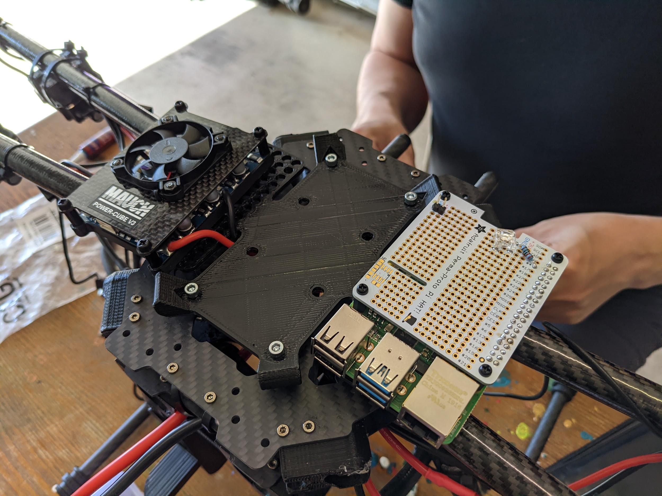
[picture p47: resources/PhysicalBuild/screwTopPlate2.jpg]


Mount pixhawk
Tape Pixhawk down to secondary top plate in corners



Glue secondary top plate to top plate with vibration gel

`@TODO need image`

== Assemble Raspberry pi

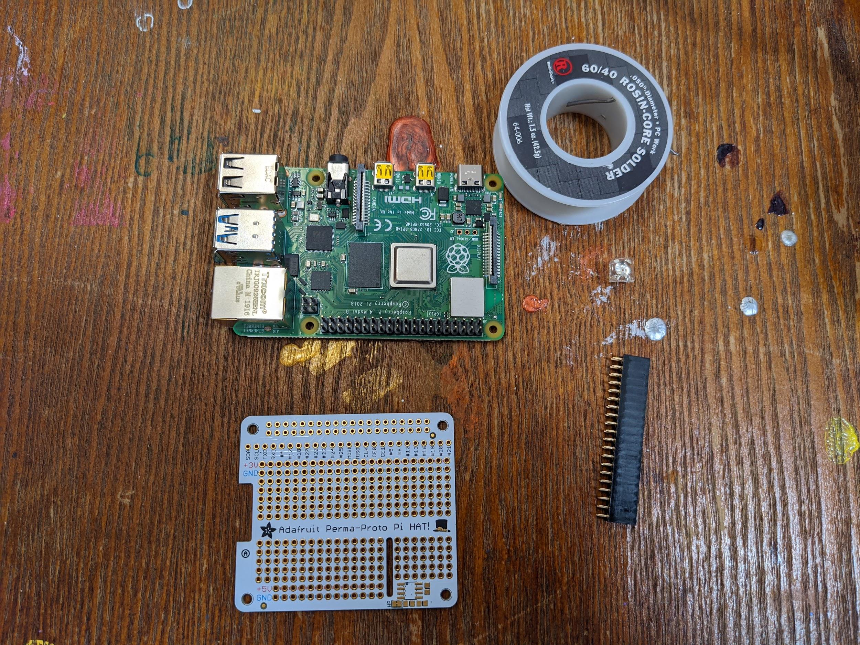
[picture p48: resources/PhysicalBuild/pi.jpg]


Solder in mounting leads

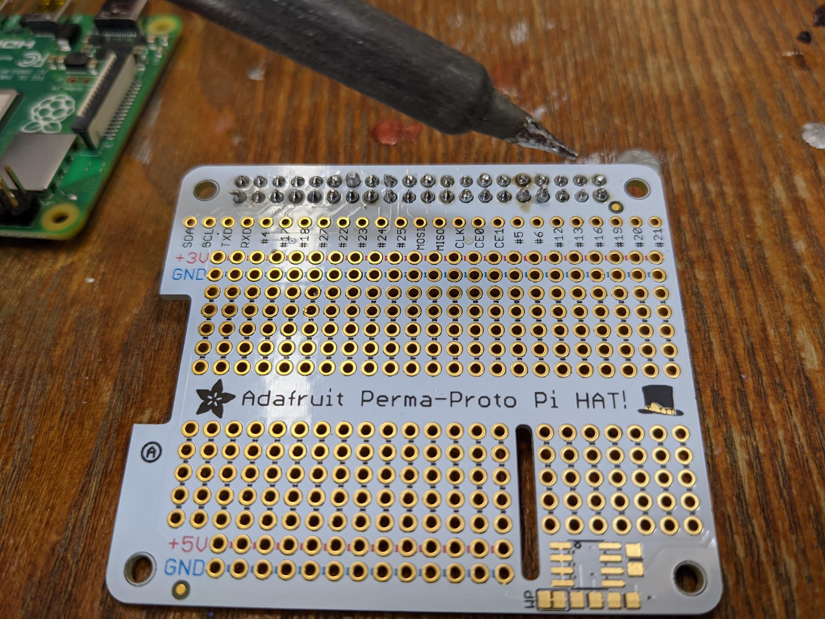
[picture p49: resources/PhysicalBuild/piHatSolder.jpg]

Wire indicator LED to hat (LED should have note facing forward)

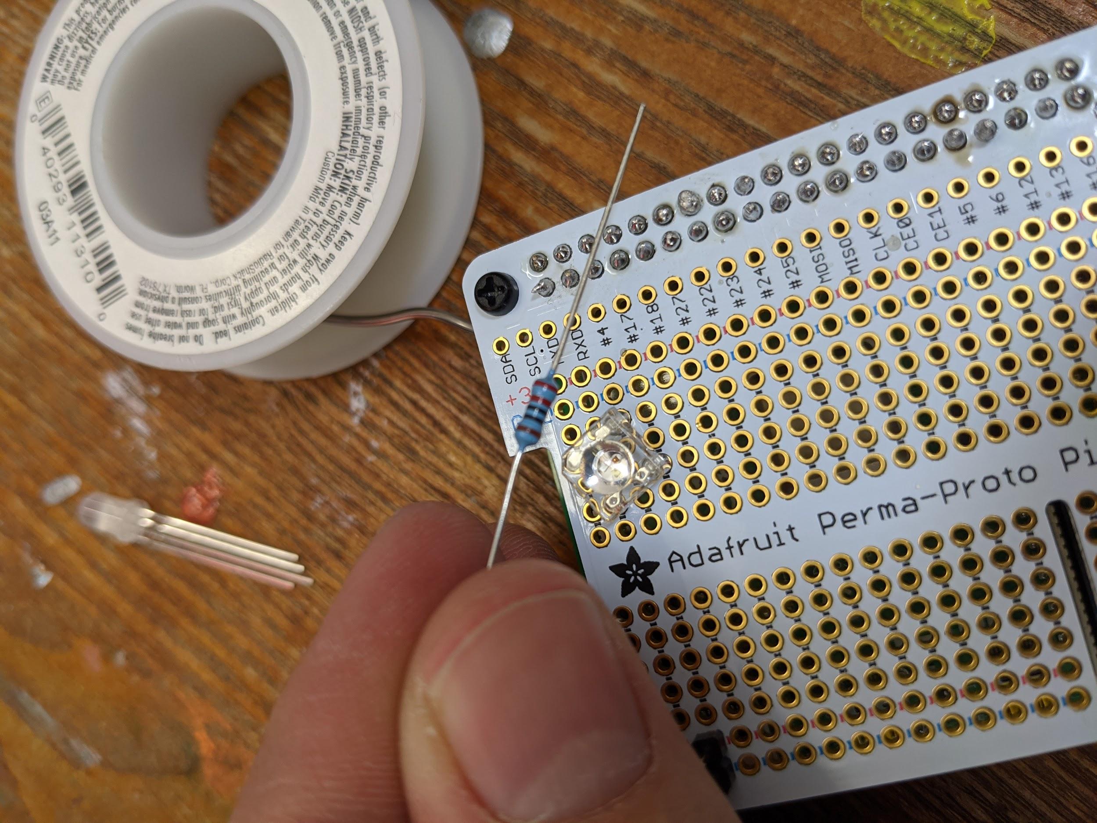
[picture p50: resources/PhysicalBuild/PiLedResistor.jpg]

Solder power jumpers

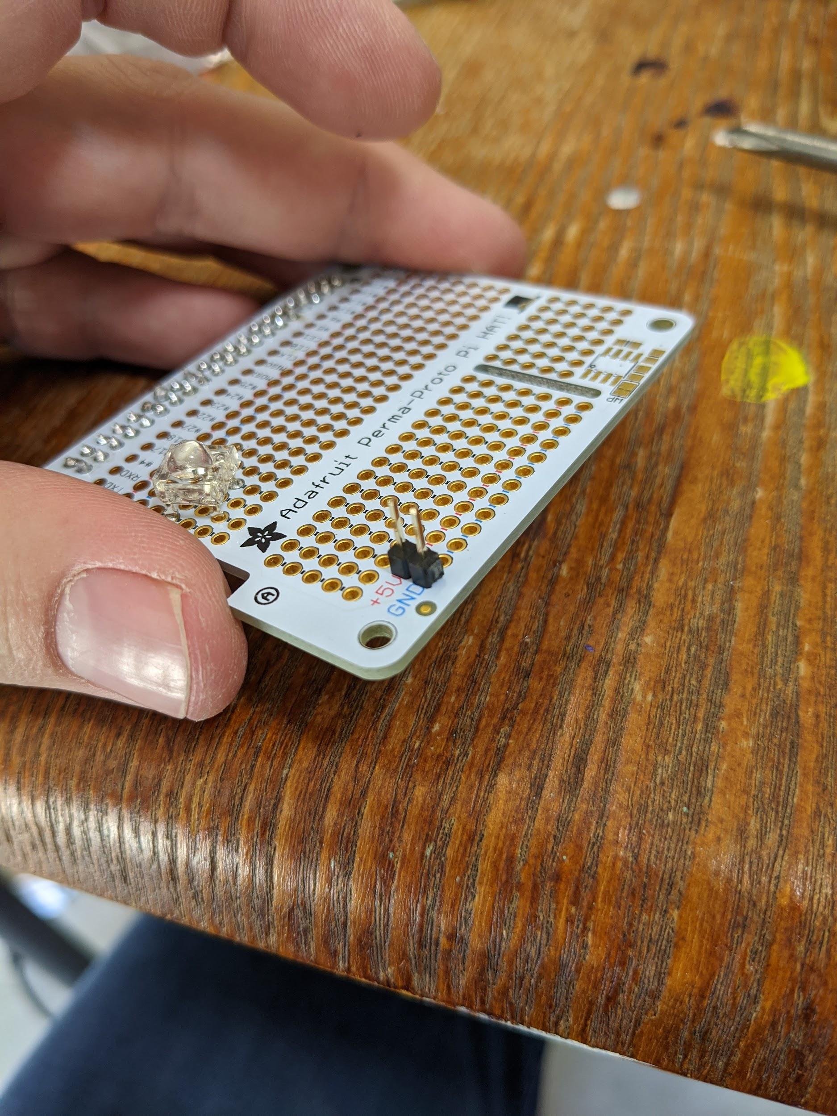
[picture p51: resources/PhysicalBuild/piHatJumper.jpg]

Attach to Raspperry PI using plastic standoffs

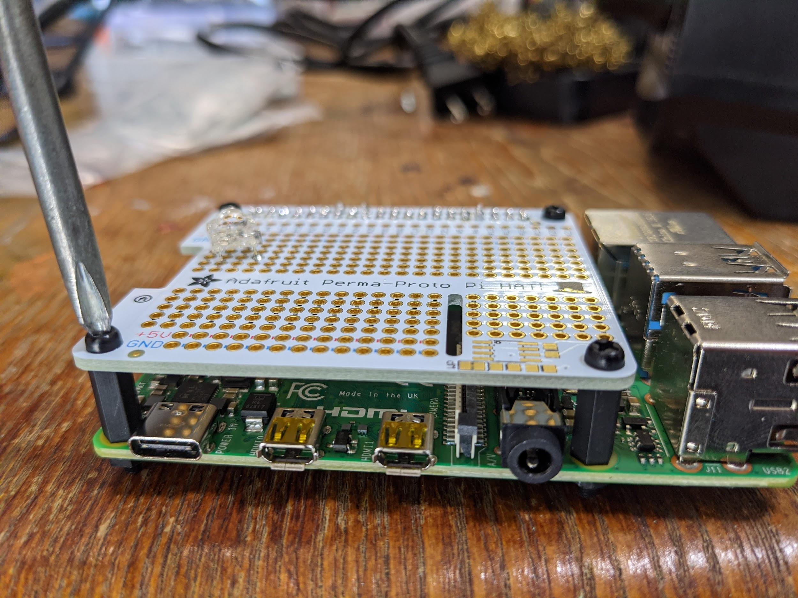
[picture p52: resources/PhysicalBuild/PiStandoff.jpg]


Ziptie down Raspberry pi
Use large ziptie as “belt”, second small ziptie in corner


Ziptie down mauch power supply
Small zip ties in 4 corners


Wire mauch to pixhawk power 1 and power 2


`@TODO double check this image`

Mount power button and wire to Mauch


Wire hall effect sensor (voltage sensor) to Mauch

`@TODO need image`

Run ESC control lines to pixhawk
The motor orientation shoudl already be set, but wiring the control lines tot he pixhawk must be done in the specified order: [A,C,D,B] -> [1,2,3,4]

https://ardupilot.org/copter/docs/connect-escs-and-motors.html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

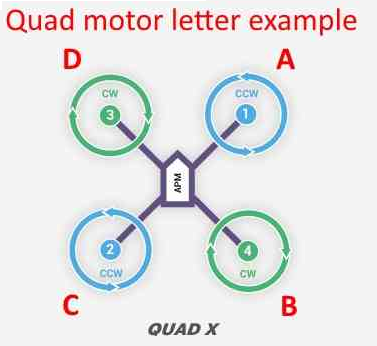
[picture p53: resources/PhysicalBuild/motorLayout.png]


Wire telemetry and radio control to pixhawk, velcro to the bottom

`@TODO need image`

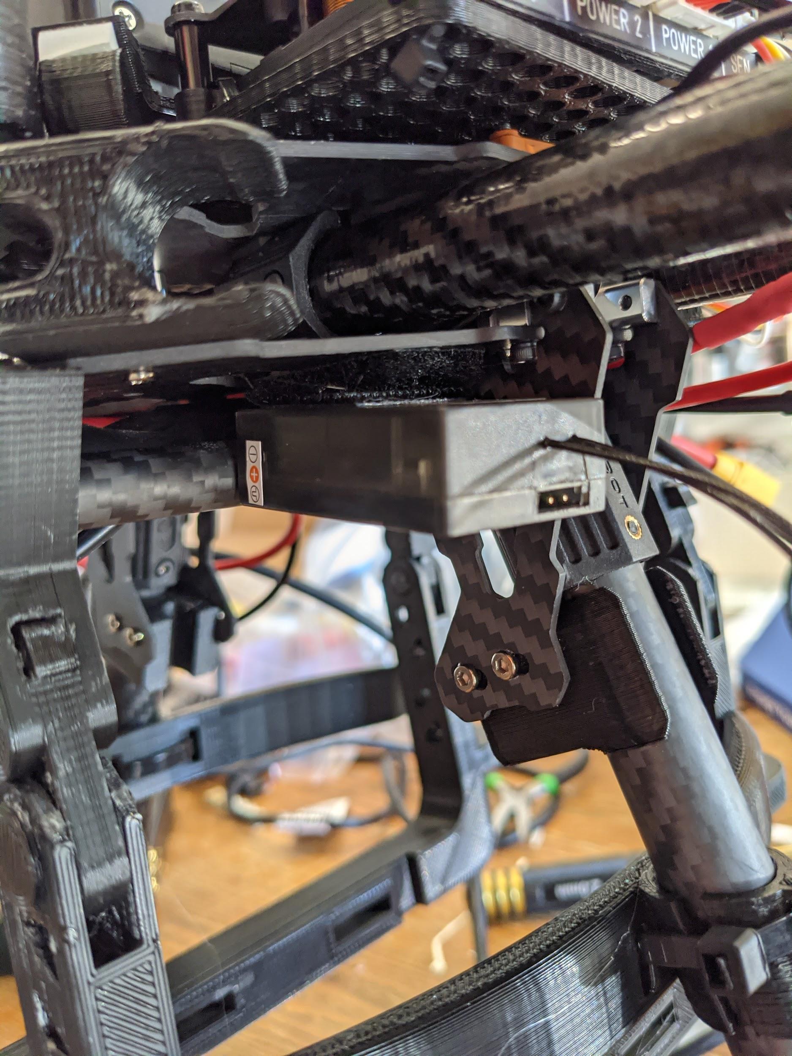
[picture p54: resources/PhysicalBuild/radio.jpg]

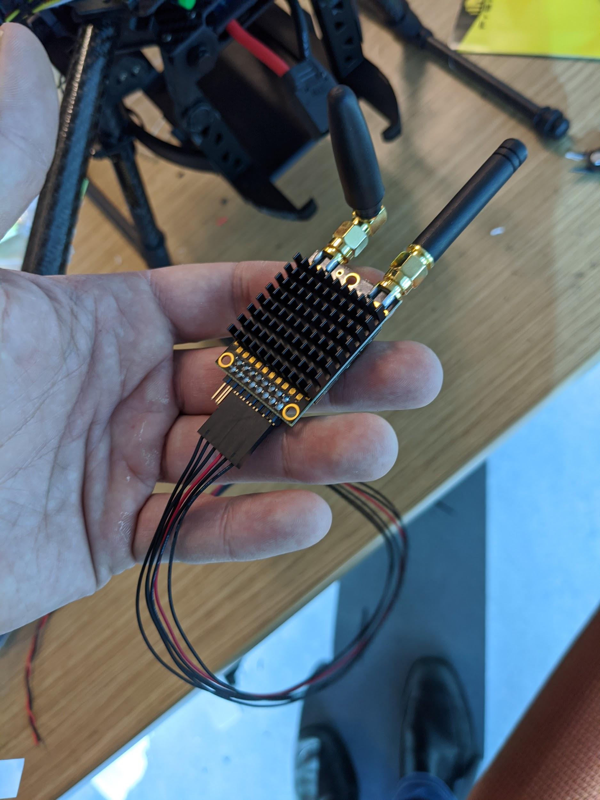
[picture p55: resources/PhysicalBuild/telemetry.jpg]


== GPS
`@TODO update images for new GPS MAST`

Assemble GPS stand and mount to front corner of frame
Glue together GPS stand structure.  Verify length will fold down accommodating GPS wire length.

`@TODO need image for GPS wire length`

Attach stand structure to the bottom bracket (add tightener before screwing together):

Mount bottom bracket to the frame.  Keep in mind the orientation of the bolt and angle of the GPS arm.  The arm should tilt in towards the center but face forward and the bolt should face outward for accessibility.  Be sure to add Loctite

Mount GPS device

Wire to Pixhawk GPS, lidar, etc

Wire to raspberry pi pixhawk uart, sba5 usb

Wire in LiDAR

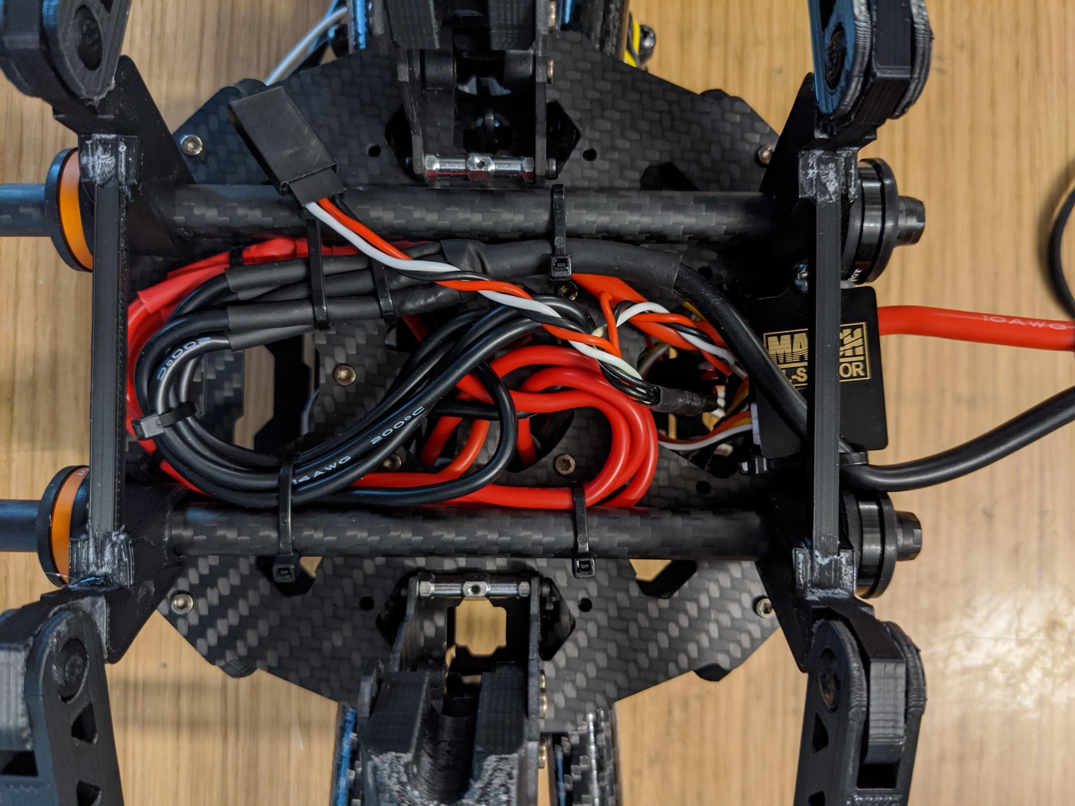
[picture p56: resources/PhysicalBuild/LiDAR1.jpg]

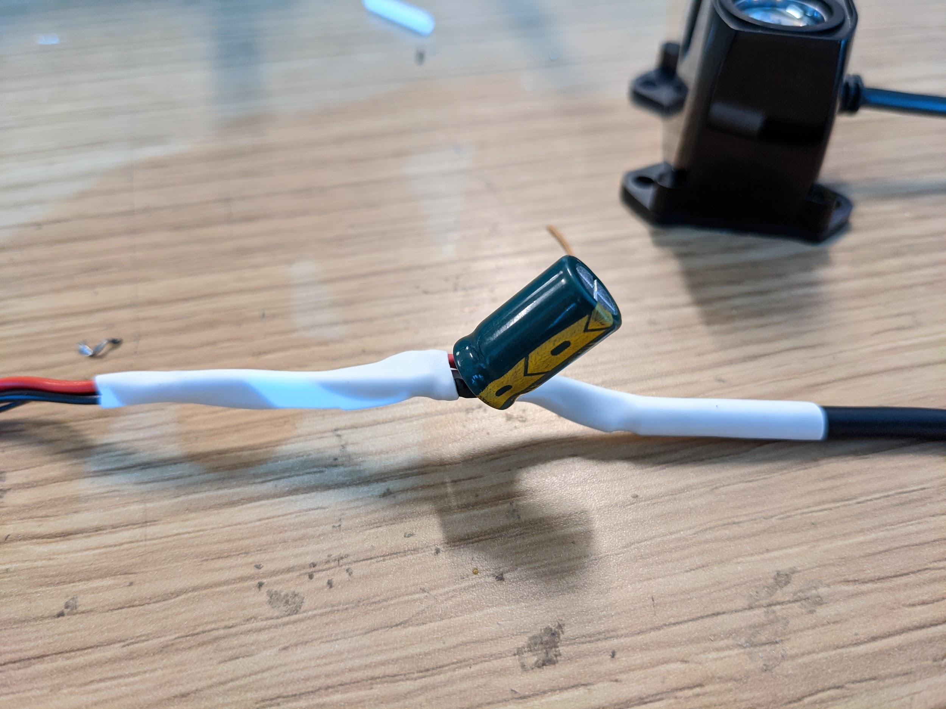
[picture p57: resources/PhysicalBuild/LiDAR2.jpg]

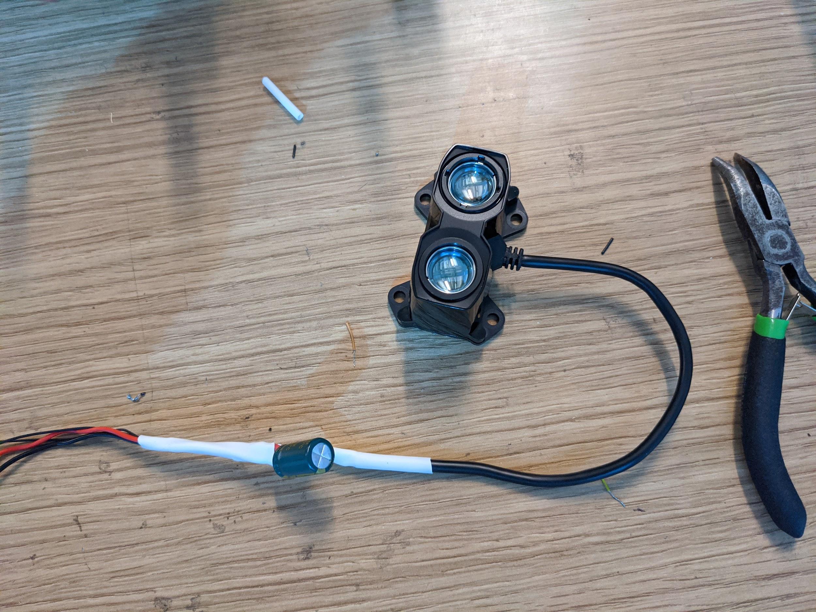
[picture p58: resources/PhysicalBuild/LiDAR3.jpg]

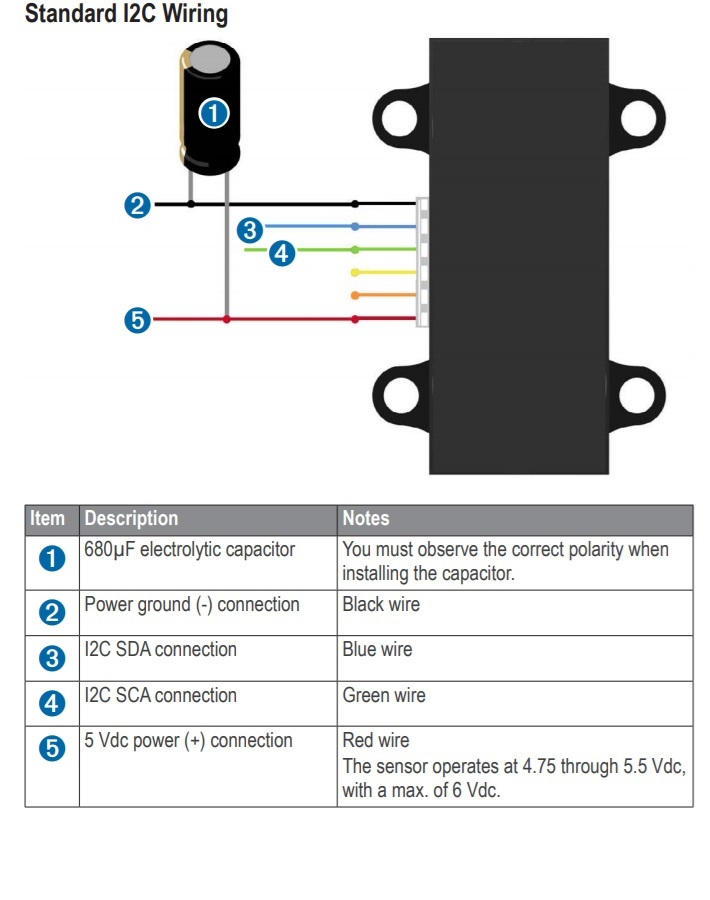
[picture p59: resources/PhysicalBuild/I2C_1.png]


https://docs.px4.io/v1.9.0/en/sensor/lidar_lite.html

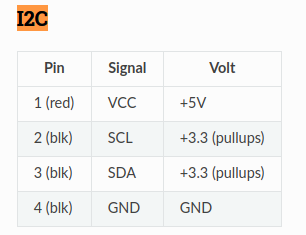
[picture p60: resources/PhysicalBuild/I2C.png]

https://ardupilot.org/copter/docSebas/common-pixhawk-overview.html#i2c

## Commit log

2022-06-07 resources/3DPrintedParts/ESCMount.png: update to new version longer legs
2022-06-07 resources/3DPrintedParts/MotorMount.png: remove old part
2022-06-07 3DPrintedParts.adoc: remove old part, add arm fulcrum
2022-06-07 resources/3DPrintedParts/stl/Arm Fulcrum.stl: add most of the stls
    [Arm Fulcrum.stl, Arm Lock Lock.stl, Axil.stl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]
2022-06-07 resources/3DPrintedParts/stl/Motor Mount Top.stl: update to longer legs
    [Motor Mount Top.stl]
2022-06-28 resources/stl/Flight Controller - Bottom|Top.stl: add stls
    [Flight Controller - Bottom.stl]
2022-06-28 resources/3DPrintedParts/stl/LIDAR Lite v4 HP Holder.stl: add stl
    [LIDAR Lite v4 HP Holder.stl]
2022-08-04 resources/PhysicalBuild/ESC/*.jpg: added ESC mod images
2022-08-04 PhysicalBuild.adoc: added images and instructions for ESC mod
2022-08-04 resources/PhysicalBuild/Legs/legSetScrew*.jpg: added images
2022-08-04 PhysicalBuild.adoc: added leg set screws
2022-08-04 resources/PhysicalBuild/Arms/*.jpg: Motor mount image
2022-08-04 PhysicalBuild.adoc: added motor mount images
2022-08-07 Updated arm and body build instructions and pictures
2022-08-08 SoftwareInstallationSetup.adoc: updated for new ancible & mount edit files process
2022-09-20 resources/PhysicalBuild/motorLayout.png: remove quad+
